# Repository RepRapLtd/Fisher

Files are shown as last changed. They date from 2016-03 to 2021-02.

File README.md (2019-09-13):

# Fisher Delta 3D printer
RepRap Fisher Delta 3D printer design files
Repository includes all design files for the current Fisher Delta 3d printer kit designed by [eMAKER](https://emaker.io/product/fisher-3d-printer-kit/) and manufactured and sold by [RepRapLtd](https://reprapltd.com/product-category/3d-printers/).

Organised into the following folders:

* sw/ Original design files in Solidworks 2016 format. The latest design is in FreeCAD.
* stl/ Printable files.
* dxf/ Lasercut files.
* step/ Designs in ISO STEP format.
* FreeCAD/ Designs for the FreeCAD CAD system.
* InDevelopment/ What it says...
* Legacy/ Old files no longer current.
* SoftwareXXX/ Current firmware as a compiled .bin file from [David Crocker](https://github.com/dc42/RepRapFirmware/releases) and [Duet3d](https://duet3d.dozuki.com/Wiki/Firmware_Overview) plus SD card images.

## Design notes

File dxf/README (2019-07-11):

Editing .dxfs
-------------

Before save:

  1. Select all.
  2. Modify attributes-
       Layer: 0
       Colour: Black/white
       Line width: 0.15mm
       Line type: continuous
  3. Save

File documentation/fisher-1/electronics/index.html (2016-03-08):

# Electronics

# Side panel wiring

You will need the following parts:

# | Component | Qty | Type

1303 | Side Panel | 1 | Laser cut
242 | M3x16mm cap head screw | 6 | Fastener
185 | Microswitch | 2 | Electronics
133 | Cable ties 2mm | as needed | Electronics
585 | Hot end loom – 1190mm | 1 | Wiring
1198 | End stop loom – 500mm | 1 | Wiring
552.1 | End stop loom – 600mm | 1 | Wiring
1199 | End stop loom – 800mm | 1 | Wiring
789 | Motor wiring loom – 500mm | | Wiring

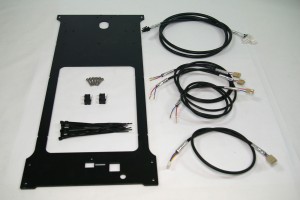
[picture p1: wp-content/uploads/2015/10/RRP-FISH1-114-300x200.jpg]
RRP-FISH1-114

(http://emaker.github.io/Fisher/wp-content/uploads/2015/10/hot-end-loom-components.jpg)

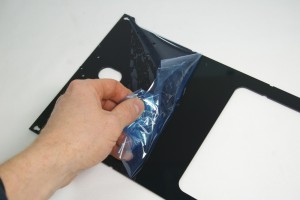
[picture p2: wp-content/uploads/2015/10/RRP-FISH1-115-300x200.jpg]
RRP-FISH1-115
Remove the protective film from the acrylic panel. | 
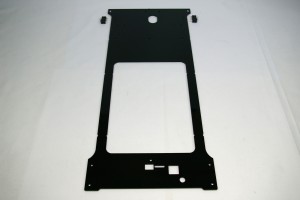
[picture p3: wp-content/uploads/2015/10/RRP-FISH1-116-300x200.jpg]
RRP-FISH1-116
The microswitches fit to the inside of the panel. Note the orientation of the bottom of the panel; this fits around the Duet electronics. | 
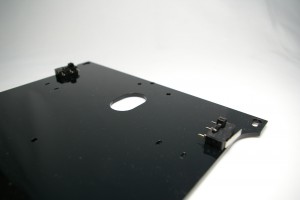
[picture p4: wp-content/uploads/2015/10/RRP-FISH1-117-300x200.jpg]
RRP-FISH1-117
Fit the microswitches with cable ties, as you did with the first microswitch. Make sure the cable tie end is towards the top of the panel. | 
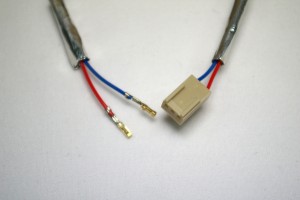
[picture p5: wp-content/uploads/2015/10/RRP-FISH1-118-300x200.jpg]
RRP-FISH1-118
The endstop looms have two wire, and there are three different lengths. | 
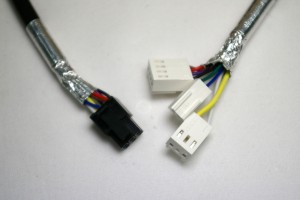
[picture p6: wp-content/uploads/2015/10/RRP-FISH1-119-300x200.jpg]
RRP-FISH1-119
The hot end loom has eight wires. | 
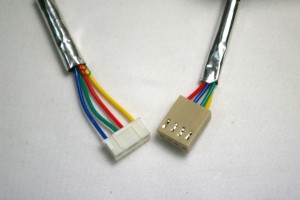
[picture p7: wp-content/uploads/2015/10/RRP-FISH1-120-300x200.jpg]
RRP-FISH1-120
The extruder motor wire has four wires. | 
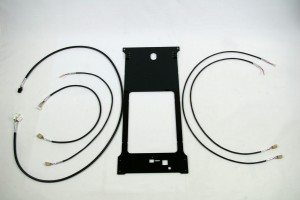
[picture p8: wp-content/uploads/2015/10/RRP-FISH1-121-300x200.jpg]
RRP-FISH1-121
Mount the shortest endstop loom, the hot end loom and the extruder motor loom on the left side. The other two endstop looms go on the right. | 
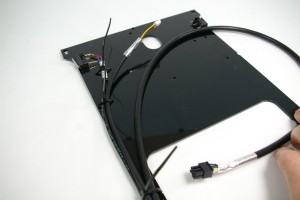
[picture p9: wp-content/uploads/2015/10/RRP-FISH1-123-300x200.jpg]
RRP-FISH1-123
Left side: Attach the endstop loom to the microswitch on the left hand side. Put the crimps on the outside tabs of the microswitch, NOT the middle one. Polarity is not important. Try not to bend the crimps on the microswitch tabs, or they will become loose. | 
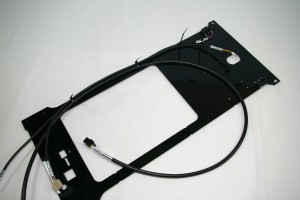
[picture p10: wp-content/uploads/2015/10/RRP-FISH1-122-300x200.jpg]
RRP-FISH1-122
Fasten the endstop loom in the top cable tie, the endstop and the extruder loom in the next one down, and all three looms in the rest of the cable ties. Don’t fully tighten the cable ties yet, so you can adjust the wire position. | 
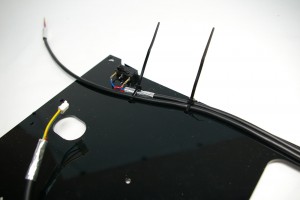
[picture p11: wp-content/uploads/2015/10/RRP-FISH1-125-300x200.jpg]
RRP-FISH1-125
Right side: connect the shorter endstop loom to the microswitch. | 
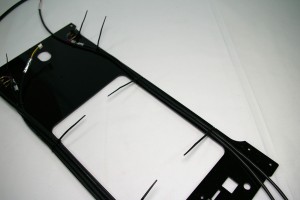
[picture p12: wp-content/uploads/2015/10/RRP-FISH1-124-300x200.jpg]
RRP-FISH1-124
Cable tie both wires in all of the positions. | 
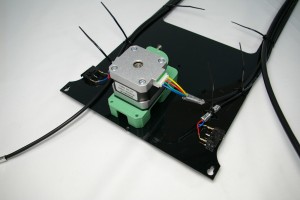
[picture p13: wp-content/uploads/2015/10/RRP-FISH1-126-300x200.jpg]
RRP-FISH1-126
Attach the extuder to the panel, with two M3x16mm cap head screws, from the outside. Connect the extruder motor loom to the extruder motor. | 

## Fit the panel and connect

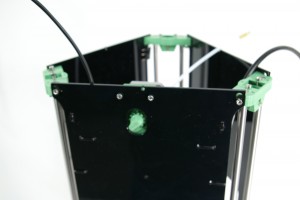
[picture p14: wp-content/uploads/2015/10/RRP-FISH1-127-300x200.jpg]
RRP-FISH1-127
As with the other panels, lift the printer up off the surface, and fit the top of the panel onto the screws in the idler printed part. | 
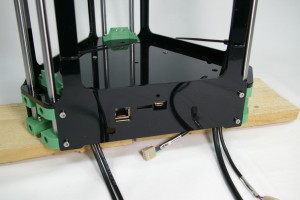
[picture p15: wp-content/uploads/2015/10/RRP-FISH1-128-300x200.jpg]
RRP-FISH1-128
Line up the bottom with the holes in the motor mounts, and fasten with four M3x16mm cap head screws. Make sure the wiring looms fit into the slots in the base plate. | 
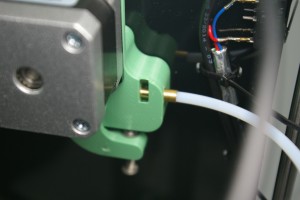
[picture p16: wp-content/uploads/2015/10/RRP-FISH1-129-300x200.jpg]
RRP-FISH1-129
Connect the Bowden tube to the extruder. Remove the tongue, and insert the brass union. | 
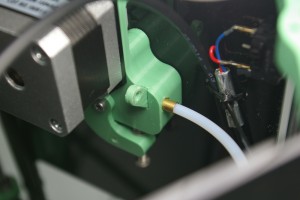
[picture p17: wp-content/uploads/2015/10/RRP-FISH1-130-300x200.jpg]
RRP-FISH1-130
Reinsert the tongue. This should engage with the slot in the brass union. | 
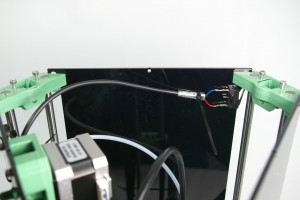
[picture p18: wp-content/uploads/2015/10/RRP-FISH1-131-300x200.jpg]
RRP-FISH1-131
Connect the third microswitch in the same way as the other two, and cable tie it to the panel. | 
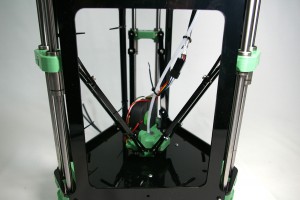
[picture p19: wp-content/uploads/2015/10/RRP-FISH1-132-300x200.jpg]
RRP-FISH1-132
Connect the hot end loom to the hot end. We find it useful to cable tie the loom loosely to the Bowden tube, above and below the connector. | 
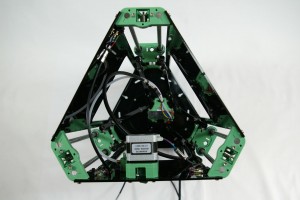
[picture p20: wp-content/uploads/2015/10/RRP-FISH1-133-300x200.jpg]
RRP-FISH1-133
Now adjust the cable lengths until everything is neat. The hot end loom and Bowden tube should move together. Try and get a nice loop, so they concertina up as the effector moves up. | 
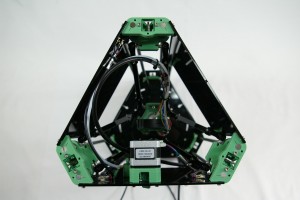
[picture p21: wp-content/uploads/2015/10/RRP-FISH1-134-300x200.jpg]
RRP-FISH1-134
Tighten and trim all of the cable ties. Move the carriages up and down their full range of movement, making sure they don’t catch on anything. Check that the heads of the cable ties don’t get in the way, and that the wiring looms are neat against the side panels. Adjust any cables as needed, and make sure the hot end loom and Bowden tube don’t catch on anything. | 

# Bed probe wiring

You will need the following parts:

# | Component | Qty | Type

1203 | Bed probe loom | 1 | Wiring
1202 | Bed probe wire | 2 | Wiring
242 | M3x16mm cap head screw | 6 | Fastener
212 | M3 washer | 6 | Fastener
1253 | M3x8mm spacer | 6 | Hardware

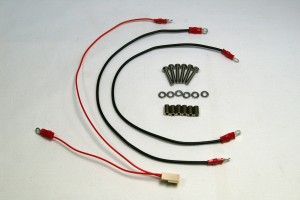
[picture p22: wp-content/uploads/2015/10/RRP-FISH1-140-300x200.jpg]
RRP-FISH1-140


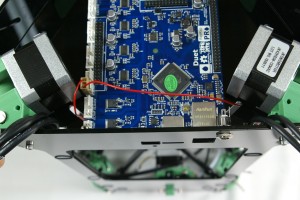
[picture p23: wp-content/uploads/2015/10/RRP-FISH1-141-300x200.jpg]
RRP-FISH1-141
Fit the bed probe loom 3-way connector to the E-stop header on the Duet. Push the wires through the slots in the base, as shown. The long wire can go under the Duet, if you prefer. | 
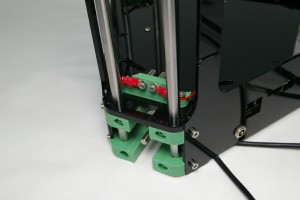
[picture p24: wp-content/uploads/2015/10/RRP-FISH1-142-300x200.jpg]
RRP-FISH1-142
Attach the ring terminals of the bed probe loom and bed probe wires to the bed mounting brackets. For each connection, the order is M3x16mm cap head screw, ring terminal of loom, bed mounting bracket, M3 washer, round spacer. | 
View from the front of the bed mounting bracket. | RRP-FISH1-143
Repeat the above steps for all six connections. The circuit goes around the circle. The balls on the print surface will complete the circuit (see later). When the nozzle pushes down on the bed, the circuit is broken. This calibrates the nozzle height. | RRP-FISH1-144

# Fit the power jack

You will need the following parts:

# | Component | Qty | Type

193 | Power jack | 1 | Electronics
455 | Power jack nut | 1 | Electronics

RRP-FISH1-138

Turn the printer over. It can rest on it’s top as you connect the wiring. The DC power jack may now be fitted as shown, next to the ethernet socket. | RRP-FISH1-139

# Duet connections

## Wiring diagram

The instructions below show the fitting of the wiring. If in doubt, refer to this wiring diagram.

FISHER-1-Duet0.6-109

## Duet wiring connections

Connect the wiring looms to the Duet, as shown in the pictures below (click on any picture for a larger version). Also refer to the wiring diagram, above. You will need the following parts:

# | Component | Qty | Type

1201 | DC cable – 250mm | 1 | Wiring
477 | Motor loom – 160mm | 1 | Wiring
478 | Motor loom – 90mm | 2 | Wiring

RRP-FISH1-145

FAN0 – NO CONNECTION! Do not connect anything to the first two pins on the left. They are not used on the Fisher. | RRP-FISH1-146
E0_TEMP – Hot end thermistor (green/blue, 2-way) | RRP-FISH1-147
E0_HEATER – Hot end heater (black/purple/red/brown, 4-way) | RRP-FISH1-148
– Hot end fan (yellow/none/white, 3-way) NOTE: this connects to the double row of pins, NOT to ‘FAN0’. From the left, there should be two clear pins, then the yellow wire, another pin (covered by the housing, but not connected), then the white wire. | RRP-FISH1-149
E0_MOT/STOP – (on first three pins) Bed probe (red/blank/red, 3-way). This was already fitted in the bed probe wiring step. | RRP-FISH1-149
E0_MOT/STOP – (on the other four pins) Extruder drive motor (yellow/green/blue/red, 4-way) | RRP-FISH1-150
X_MOT/STOP – X endstop (blue, space, red, 3-way) This is the SHORTEST endstop loom. | RRP-FISH1-151
X_MOT/STOP – (on the other four pins) X motor (black/green/blue/red, 4-way) Now connect the X motor to the Duet, using a 90mm motor loom. This is the motor closest to the motor connection pins on the Duet. Check that the endstop at the top of this tower is the one connected next to the X motor. | RRP-FISH1-152
Y_MOT/STOP – Y endstop (blue, space, red, 3-way) This is the LONGEST endstop loom. | RRP-FISH1-153
Y_MOT/STOP – (on the other four pins) Y motor (black/green/blue/red, 4-way) Next the Y motor, using a 90mm motor loom. This is the motor nearest the large screw terminals on the end of the Duet board. Check that the endstop at the top of this tower is the one connected next to the Y motor. | RRP-FISH1-154
Z_MOT/STOP – Z endstop (blue, space, red, 3-way) This is the MEDIUM length endstop loom. | RRP-FISH1-155
Z_MOT/STOP – (on the other four pins) Z motor (black/green/blue/red, 4-way) Now the Z motor, using the 160mm motor loom. This is the motor nearest the ethernet socket on the Duet. Check that the endstop at the top of this tower is the one connected next to the Z motor. | RRP-FISH1-157
All the wiring connections fitted. | RRP-FISH1-156
This picture shows the motor connections, and orientation. If you have put the motor on the wrong way around, you can turn the motor around, to make the motor wiring easier. Unscrew the four motor screws, and turn the motor around, then retighten the screws. | RRP-FISH1-158
Finally, connect the DC power cable. One of the cores has a black stripe running along it’s length. Connect this to the negative terminal (on the left hand side as viewed in the photograph). | RRP-FISH1-159
Connect the DC power cable to the tabs on the back of the jack. | RRP-FISH1-160
Ground is the centre of the three tabs (the wire with the black stripe should connect to this), and positive is the tab that connects to the centre pin. Fit them with the ‘curly’ part of the crimp outwards. | HUX2-electronics-25
With all the wiring fitted, tidy up the wiring so that it all fits below the level of the acrylic side panels. You can use a couple of cable ties to help. | RRP-FISH1-161

# Jumper

You will need the following parts:

# | Component | Qty | Type

| Fisher | 1 | Part-assembled
285 | PCB Jumper | 1 | Electronics

RRP-FISH1-162

Fit the jumper onto the 5V_EN (JP9) header pins (location highlighted in the picture). This uses the on-board 5V regulator to supply power to the main processor of the Duet, when 19V power is connected. | RRP-FISH1-163
A close up of the jumper position. | RRP-FISH1-164

Fisher Delta 3D printer © 2016. All Rights Reserved.

Powered by WordPress (http://www.wordpress.org). Designed by Woo Themes (http://www.woothemes.com)

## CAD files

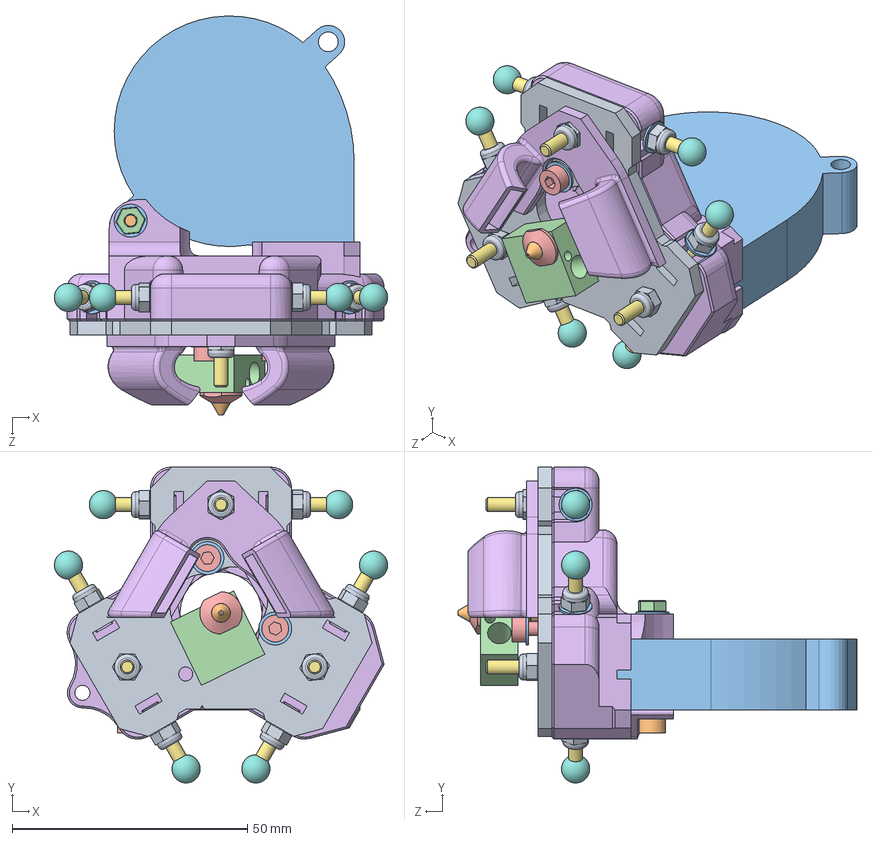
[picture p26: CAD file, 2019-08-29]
sw/head.sldasm
70.8 x 67.2 x 84.8 mm
heater-block

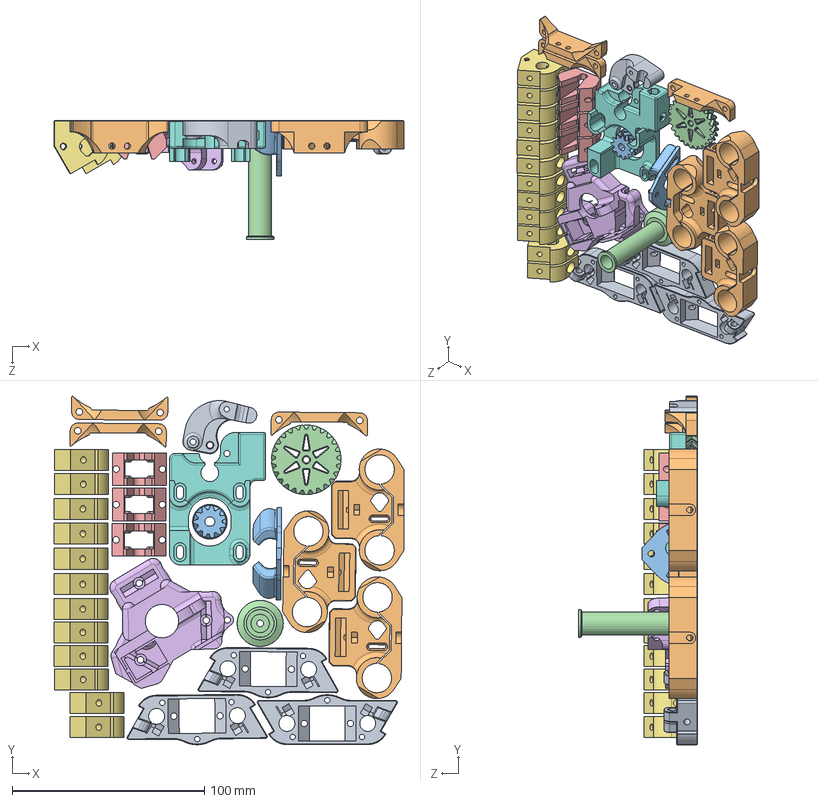
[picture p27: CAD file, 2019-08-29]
sw/1312.SLDASM
181.9 x 181.2 x 62.0 mm

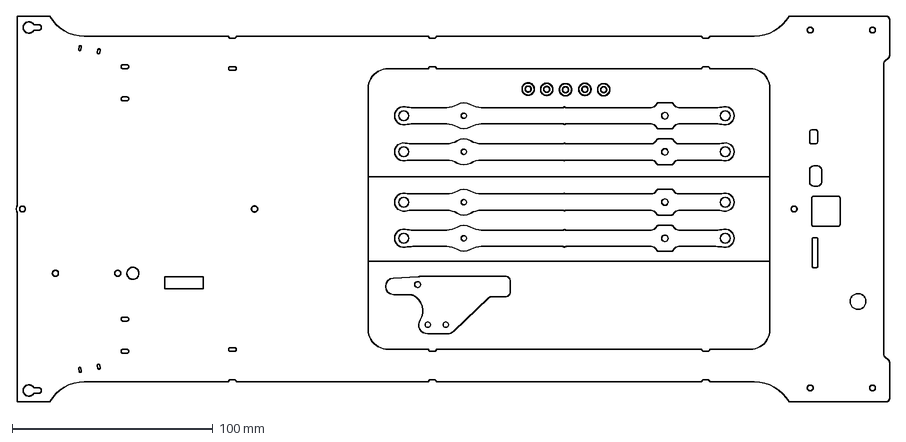
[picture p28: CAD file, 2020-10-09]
dxf/1196.3.dxf
434.6 x 192.0 mm

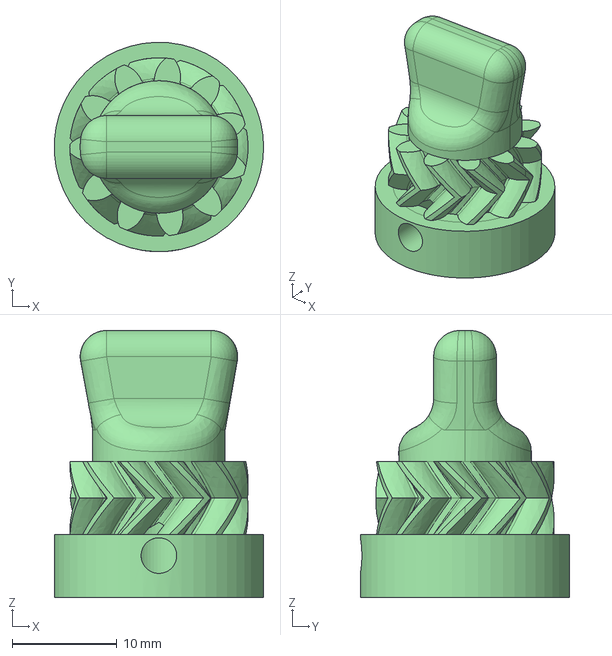
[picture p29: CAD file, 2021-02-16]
FreeCAD/1310.2.FCStd
20.0 x 20.0 x 25.5 mm

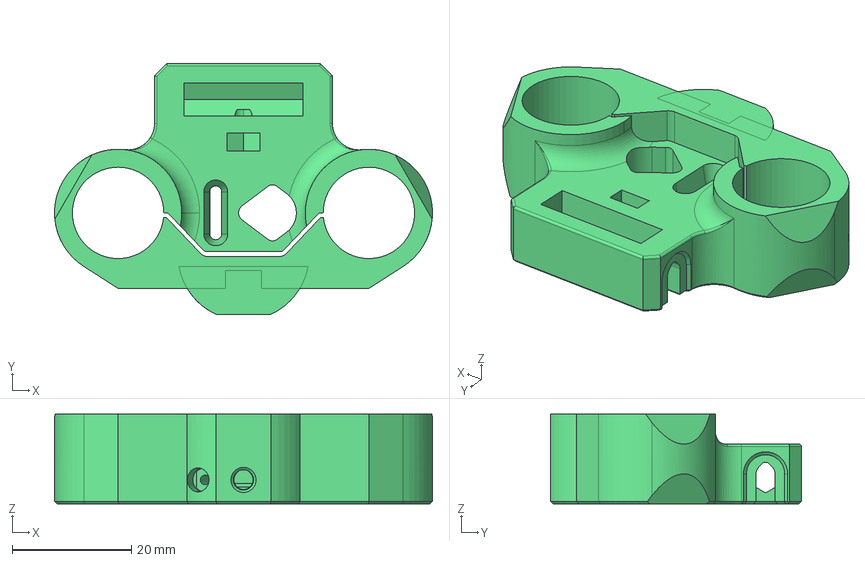
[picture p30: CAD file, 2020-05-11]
InDevelopment/Mechanics/1304.2.FCStd
63.3 x 42.0 x 15.0 mm

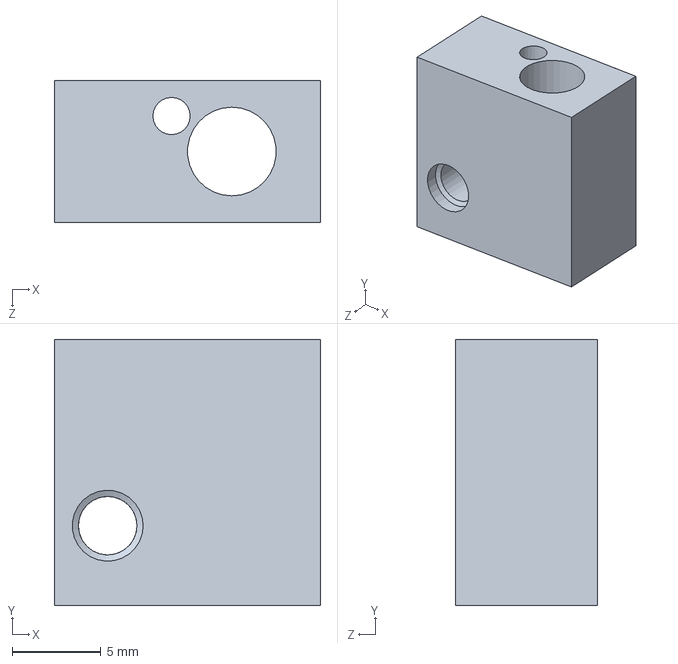
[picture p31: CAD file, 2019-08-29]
sw/heater-block.SLDPRT
15.0 x 15.0 x 8.00 mm

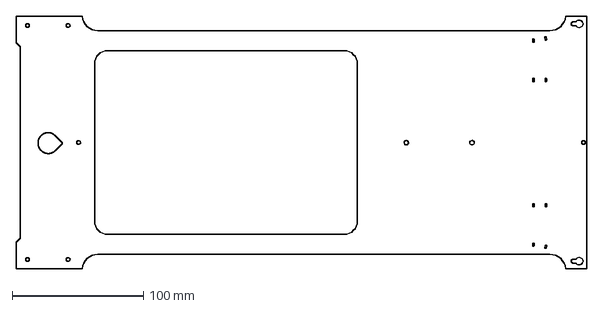
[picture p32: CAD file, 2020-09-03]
dxf/#1302.1.dxf
434.2 x 192.1 mm

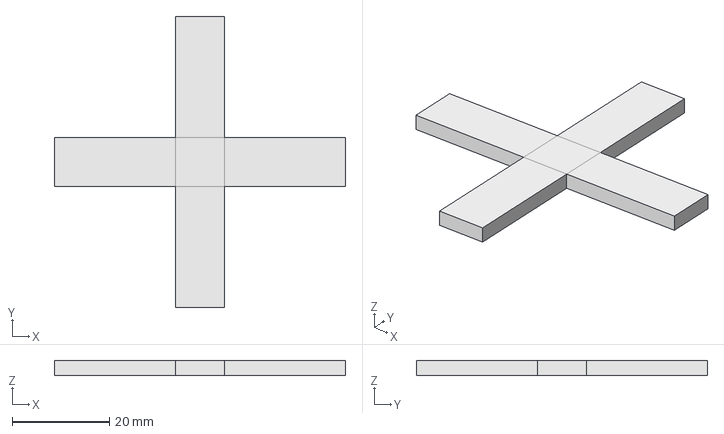
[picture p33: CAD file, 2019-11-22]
FreeCAD/test-cross.fcstd
60.0 x 60.0 x 3.00 mm

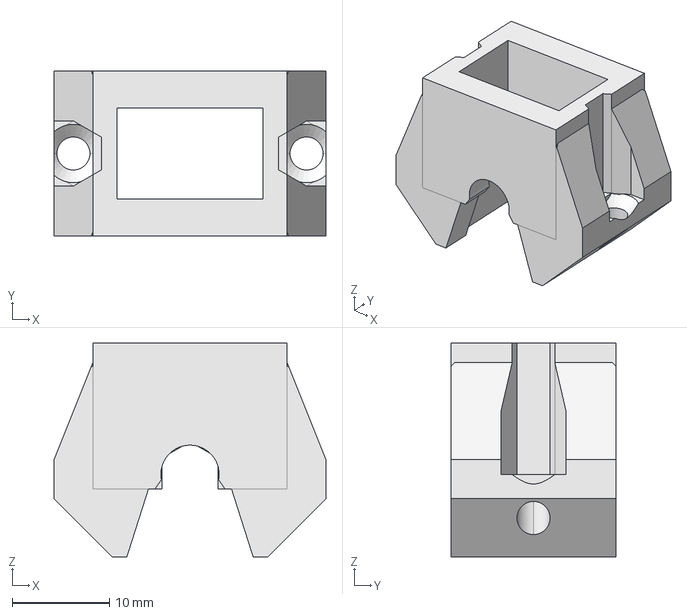
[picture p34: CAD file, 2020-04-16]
InDevelopment/Mechanics/1243.1.FCStd
28.0 x 17.0 x 22.0 mm

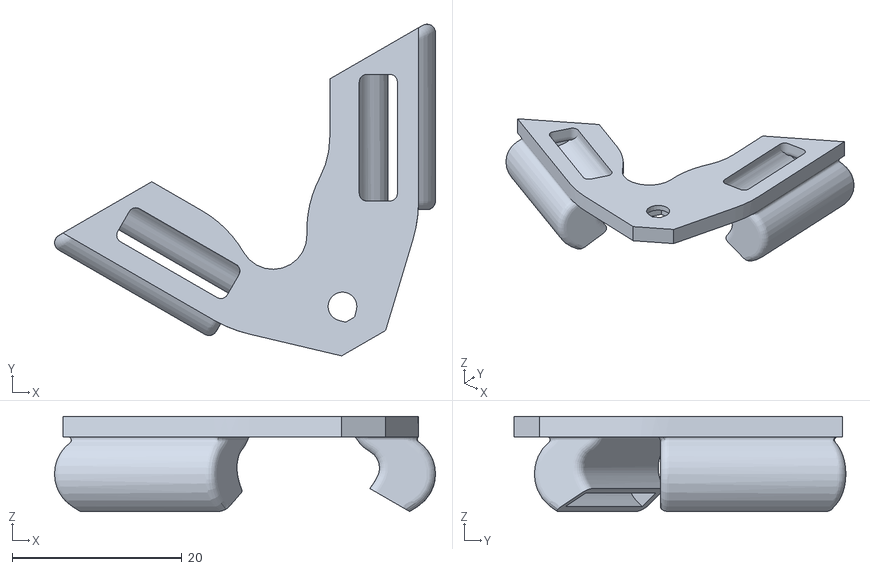
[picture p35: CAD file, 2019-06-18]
stl/1247.1 Nozzle Duct.stl
45.0 x 39.1 x 11.2

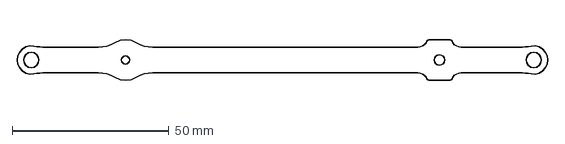
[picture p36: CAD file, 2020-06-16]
dxf/1232.2.dxf
169.5 x 13.6 mm

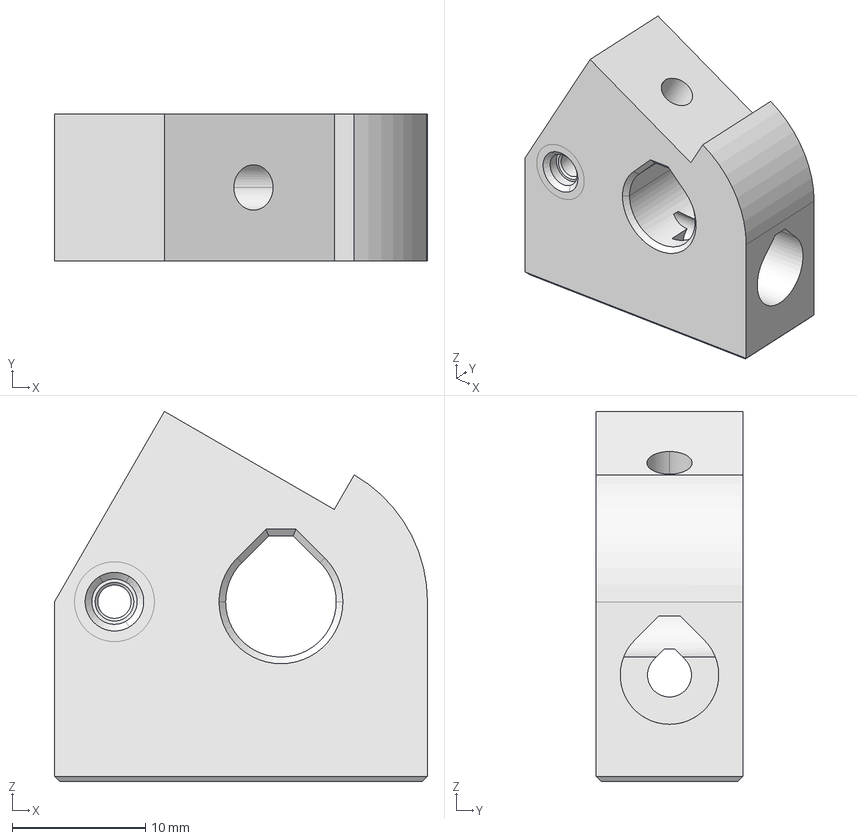
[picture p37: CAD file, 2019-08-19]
FreeCAD/1305.1.fcstd
28.0 x 11.0 x 27.8 mm

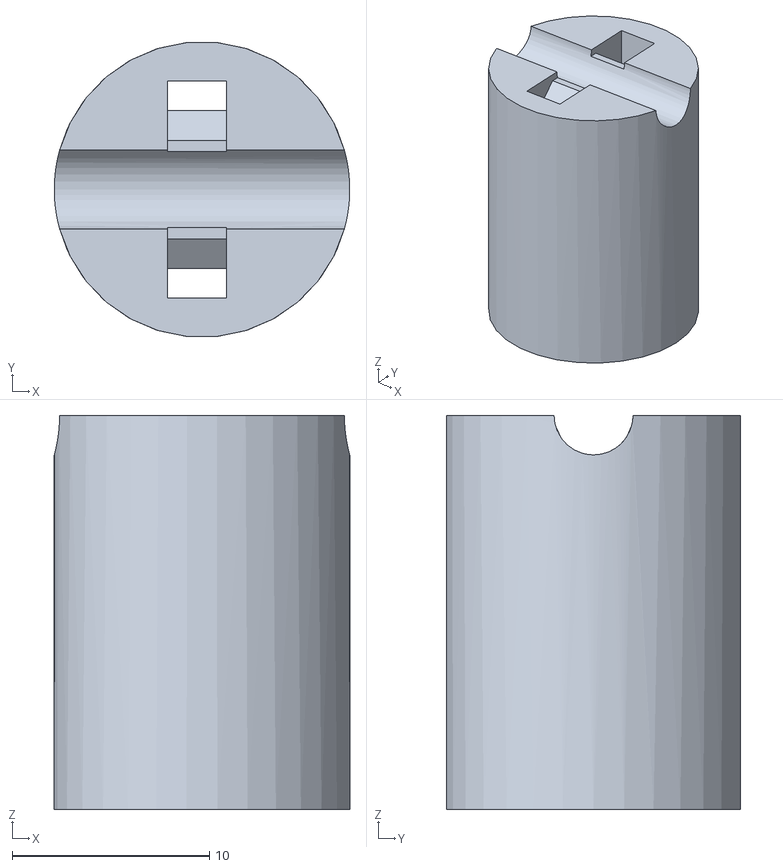
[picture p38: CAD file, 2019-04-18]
stl/6199-filament-guide-spacer.stl
15.0 x 14.9 x 20.0

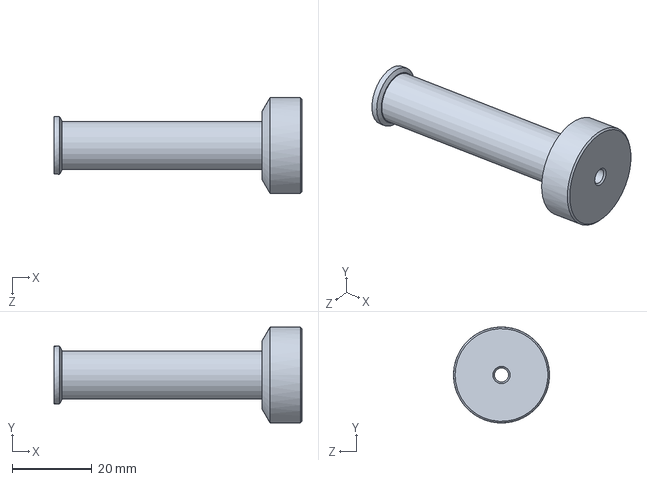
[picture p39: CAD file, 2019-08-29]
sw/1249.SLDPRT
62.0 x 24.0 x 24.0 mm

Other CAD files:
stl/1310.2-small-gear with grip.STL
dxf/1195.3.dxf
FreeCAD/6197 masterspool-spigot.fcstd
stl/1310.1-small-gear with grip.STL
InDevelopment/Mechanics/STLs/1243.1.stl
InDevelopment/Mechanics/STLs/1304.2.stl
Legacy/Old DXF/#1195 - 05.DXF
Legacy/Old DXF/#1223.DXF
Legacy/Old DXF/1195 - 05 - single.DXF
Legacy/Old DXF/1195 - 05.DXF
Legacy/Old DXF/1195.1.dxf
Legacy/Old DXF/1195.2.dxf
Legacy/Old DXF/1196 - 07 - single.dxf
Legacy/Old DXF/1196 - 07.dxf
Legacy/Old DXF/1196.1.dxf
Legacy/Old DXF/1232-fisher-rods-x2.dxf
Legacy/Old DXF/1232.1-fisher-rods-x2.dxf
Legacy/Old DXF/1232.1-fisher-rods-x6.dxf
Legacy/Old DXF/1232.1.dxf
Legacy/Old DXF/1232.DXF
Legacy/Old DXF/1302.DXF
Legacy/Old DXF/1303.DXF
Legacy/Old-STL/1249.STL
Legacy/Old-STL/1305.STL
Legacy/Old-STL/rod-end.STL
Legacy/old-sd-image/stl/Robot.stl
dxf/#1195 - 05.DXF
dxf/#1223.DXF
dxf/1195 - 05 - single.1.dxf
dxf/1195 - 05 - single.DXF
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

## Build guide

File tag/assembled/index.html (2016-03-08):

# Tag Archives: Assembled

 (http://emaker.github.io/Fisher/author/jeanmarc/) Nov 20 2015

# Assembled Fisher Delta 1.0 for Christmas (http://emaker.github.io/Fisher/assembled-fisher-delta/)

- Fisher 1 (http://emaker.github.io/Fisher/category/fisher-1/), News (http://emaker.github.io/Fisher/category/news/)
- Assembled (http://emaker.github.io/Fisher/tag/assembled/), fisher (http://emaker.github.io/Fisher/tag/fisher/)
- Leave a comment (http://emaker.github.io/Fisher/assembled-fisher-delta/#respond)

We have a limited number of Assembled Fisher Delta 1.0 RepRap 3D printers available to order for dispatch in time for Christmas – So get your order in quick! For a special price of £449 (ex VAT) you will receive a fully built Fisher 1.0 which has been commissioned and tested. The assembled kits will […]

Fisher Delta 3D printer © 2016. All Rights Reserved.

Powered by WordPress (http://www.wordpress.org). Designed by Woo Themes (http://www.woothemes.com)

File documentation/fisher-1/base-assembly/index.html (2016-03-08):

# Base assembly

# Goal

TIP: Click on pictures in the instructions to see a larger version. Right-click and select ‘Open link in new Tab’ to see the full size image.

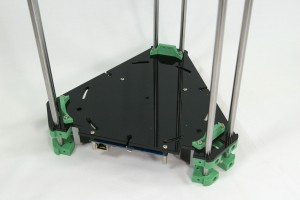
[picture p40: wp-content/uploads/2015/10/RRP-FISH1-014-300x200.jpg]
RRP-FISH1-014
By the end of this section, you will have assembled the base of the printer. | 

# Tower assembly

There are three towers, that support the three moving arms of the printer. You will need the following parts:

# | Component | Qty | Type

934 | Smooth rod 8mm x 426mm | 2 | Hardware
408 | NEMA 17 stepper motor | 1 | Hardware
1305 | Motor bracket | 4 | Printed
112 | M3x25mm cap head screw | 4 | Fastener
212 | M3 plain washer | 4 | Fastener

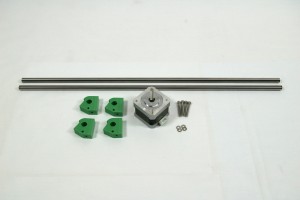
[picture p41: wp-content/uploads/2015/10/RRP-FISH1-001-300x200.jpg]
RRP-FISH1-001


TIP: There’s a list of the Fisher 1 printed parts on THIS PAGE (https://reprappro.com/documentation/fisher-1/#Printing_parts_for_Fisher). Click on the ‘Location’, to see a preview of the printed part, if you’re not sure what it is.

NOTE: The ground bars should have clean chamfered ends, free from burrs, so they can slide easily into the relevant parts without causing any damage. Check all the ground bars before proceeding and file any burrs away as necessary. You may damage the linear bearings when you fit them if you do not do this.

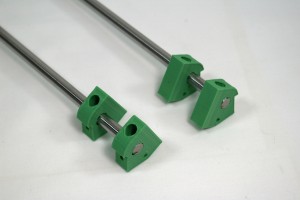
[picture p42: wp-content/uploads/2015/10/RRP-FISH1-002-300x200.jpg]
RRP-FISH1-002
Push two printed motor brackets onto the end of each smooth rod. Note the orientation, and that the bracket closest to the end of the rod should be flush with the end. | 
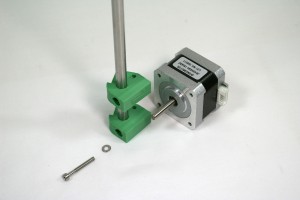
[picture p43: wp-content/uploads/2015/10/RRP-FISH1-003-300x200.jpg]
RRP-FISH1-003
Screw a M3x25mm cap head screw, through a washer and the motor bracket, and into the motor. Note that the motor wiring connector should come out sideways, not up or down. | 
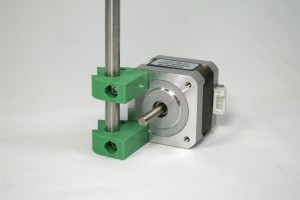
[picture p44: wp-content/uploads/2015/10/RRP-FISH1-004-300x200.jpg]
RRP-FISH1-004
Add a second M3x25mm cap head screw into the top bracket. Slide motor bracket so it lines up with the hole in the motor, and tighten. | 
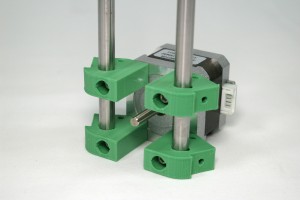
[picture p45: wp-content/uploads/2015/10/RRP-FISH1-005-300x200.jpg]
RRP-FISH1-005
Repeat for the other side. The screws and washers, when tightened, hold the rods in place so they cannot slip through the motor bracket. | 
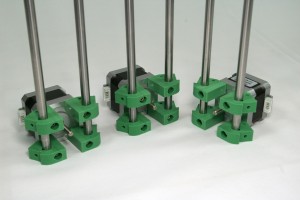
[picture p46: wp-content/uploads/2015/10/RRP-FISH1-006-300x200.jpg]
RRP-FISH1-006
You need to build three towers in total, so repeat the above twice more. You will need two with motor wiring connectors on one side, and one with it on the other side. See the picture for orientation. | 

# Base plate assembly

The base plate holds the electronics. You will need the following parts:

# | Component | Qty | Type

1299 | Base Plate (5mm acrylic) | 1 | Laser cut
744 | Duet PCB spacer (5mm acrylic, part of base plate) | 4 | Laser cut
394 | Duet PCB | 1 | Electronics
581 | Female/Female Hex Spacer | 4 | Electronics
1186 | M3x16mm button head screw | 4 | Electronics
212 | M3 plain washer | 4 | Fastener

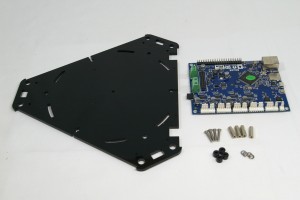
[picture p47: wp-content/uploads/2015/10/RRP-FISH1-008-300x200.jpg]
RRP-FISH1-008


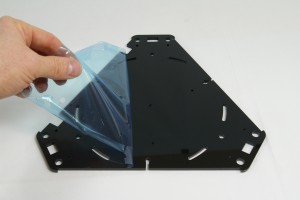
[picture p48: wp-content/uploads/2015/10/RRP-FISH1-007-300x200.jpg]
RRP-FISH1-007
All acrylic parts are covered by a protective film, on both sides. Always remove this before assembly. The Duet PCB spacers are cut into the base plate, and are attached by a small sprue. Remove them for assembly. | 
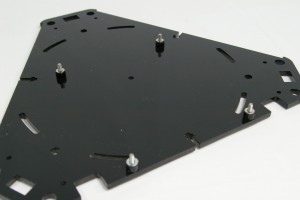
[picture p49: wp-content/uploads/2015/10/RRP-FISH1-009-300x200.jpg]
RRP-FISH1-009
There are four holes in the base plate, for mounting the Duet PCB. Push an M3x16mm button head screw through each one, and put a Duet PCB spacer and M3 washer on each on. | 
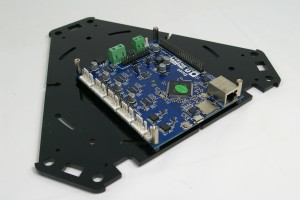
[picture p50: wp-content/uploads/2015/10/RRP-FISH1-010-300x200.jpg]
RRP-FISH1-010
Place the Duet on these, as shown. Fasten the Duet in place with the four Female/Female hex spacers. | 

# Base assembly

Assemble the lower part of the printer. You will need the following parts:

# | Component | Qty | Type

| Motor towers | 3 | Assembled
| Base | 1 | Assembled
1245 | Kinematic Mount | 3 | Printed
242 | M3x16mm cap head screw | 6 | Fastener

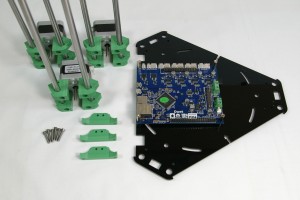
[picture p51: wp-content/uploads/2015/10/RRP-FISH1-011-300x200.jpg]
RRP-FISH1-011


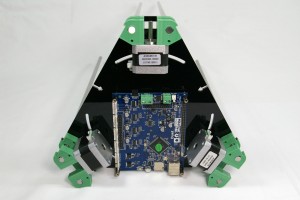
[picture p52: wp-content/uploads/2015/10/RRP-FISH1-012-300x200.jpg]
RRP-FISH1-012
Push the motors up through the base plate. Be careful to support the rods when doing this; acyrlic can be quite brittle, so you don’t want the ends to move around. Note the orientation of the motor connectors to the Duet; fit them as shown will make wiring them up much easier. | 
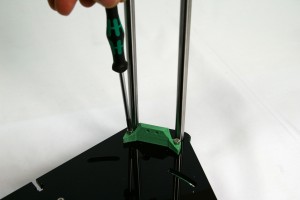
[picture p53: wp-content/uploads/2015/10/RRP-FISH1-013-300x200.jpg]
RRP-FISH1-013
Using two M3x16mm cap head screws on each, screw the three kinematic mounts onto the base plate. The screws should self-tap into the plastic of the printed motor mount underneath. | 
Your printer should now look like this. | RRP-FISH1-014

Fisher Delta 3D printer © 2016. All Rights Reserved.

Powered by WordPress (http://www.wordpress.org). Designed by Woo Themes (http://www.woothemes.com)

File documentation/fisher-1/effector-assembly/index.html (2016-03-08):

# Effector assembly

# Goal

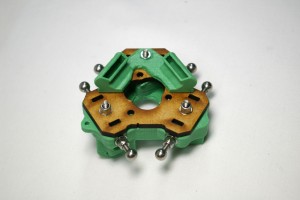
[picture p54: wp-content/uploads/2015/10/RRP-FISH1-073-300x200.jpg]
RRP-FISH1-073
By the end of this section, you will have built the effector. | 

# Effector

The effector carries the hot end, and is moved in three dimensions by the movement of the carriages on the towers. You will need the following parts:

# | Component | Qty | Type

1301 | Effector | 1 | Printed
1247.1 | Nozzle Duct | 1 | Printed
1223 | Effector Plate (MDF) | 1 | Laser cut
242 | M3x16mm cap head screw | 6 | Fastener
257 | M3x12mm cap head screw | 3 | Fastener
204 | M3 Nylock nut | 8 | Fastener
212 | M3 plain washer | 8 | Fastener
258 | M3 nut | 3 | Fastener
1191 | 6mm Threaded steel ball | 6 | Hardware

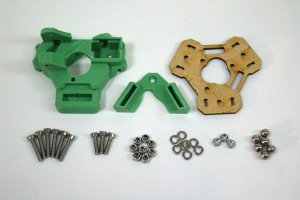
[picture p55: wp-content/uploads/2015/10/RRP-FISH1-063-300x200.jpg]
RRP-FISH1-063


## Connecting rod joints

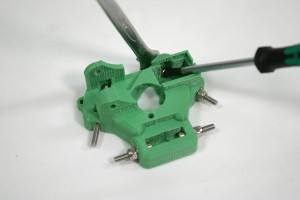
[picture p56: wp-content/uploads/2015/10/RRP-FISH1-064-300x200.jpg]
RRP-FISH1-064
Take the printed effector, and fit six M3x16mm cap head screws, each secured with an M3 washer and M3 Nylock nut, similar to the carriage. | 
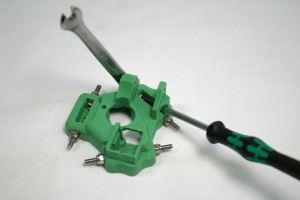
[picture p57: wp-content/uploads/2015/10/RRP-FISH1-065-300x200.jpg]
RRP-FISH1-065
Access to the M3x16mm cap head screws is possibly even more difficult than with the carriages. It really helps having a ball-ended Allen key! Tighten them as with the carriage assembly. | 
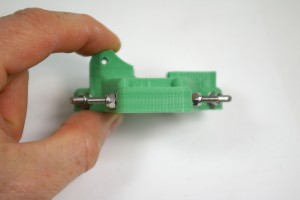
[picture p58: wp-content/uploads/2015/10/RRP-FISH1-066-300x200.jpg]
RRP-FISH1-066
As with the carriages, check that the screws are flat and straight. | 

Screw on a 6mm threaded steel ball to each side. As before, make sure the balls are free from swarf inside, and that they are threaded. Fully screw the balls on, then check that the outside measurement of the balls is close (+/- 0.25mm for best accuracy) to 56mm. You can tighten the Nyloc on the screw to pull the ball out a little, if necessary. If too wide, remove the ball and file down the screw a little, then replace the ball and measure.
NOTE: Kits supplied after 1st November 2015 have steel balls that are not tapped as deeply as previous versions. The outside measurement with these balls will be a little wider, at around 57mm.

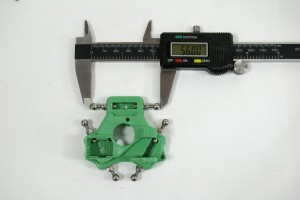
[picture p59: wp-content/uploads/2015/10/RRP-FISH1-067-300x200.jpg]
RRP-FISH1-067


The precise distance between the balls is actually not that important. What is important is that the distance between the balls on the carriage (see earlier in the instructions), and those on the effector should be the same, as close as possible. The rods that connect the carriage and effector must be parallel, so that the movement of the effector is always square to the carriage. If the distance between the balls is not the same, the rods will not be parallel, and the movement of the effector and hot end will not be consistent, and you may end up printing parts that are not dimensionally accurate.

## Effector plate

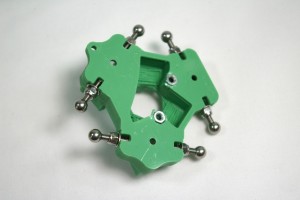
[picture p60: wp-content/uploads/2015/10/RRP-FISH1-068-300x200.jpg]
RRP-FISH1-068
Turn the effector over, and fit two M3 nuts in the captive holes underneath. | 
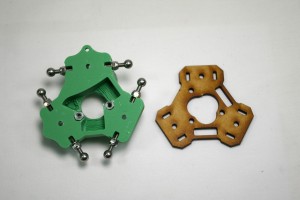
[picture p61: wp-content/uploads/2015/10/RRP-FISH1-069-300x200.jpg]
RRP-FISH1-069
Take the MDF effector plate, and orientate it so that the holes line up with M3 nuts, and duct holes match the effector. It only fits correctly one way! | 
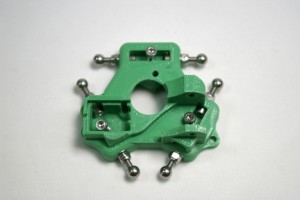
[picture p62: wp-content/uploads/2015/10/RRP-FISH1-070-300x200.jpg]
RRP-FISH1-070
From the top of the effector, put three M3x12mm cap head screws through the central holes, between the connecting rod joint screws. | 
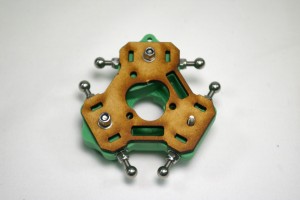
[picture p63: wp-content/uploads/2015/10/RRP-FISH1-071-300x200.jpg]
RRP-FISH1-071
Turn the effector back over, and fit the MDF effector plate, again making sure of the alignment. Use an M3 washer with M3 nylock nut on two of the screws, as shown. | 
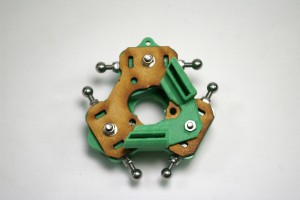
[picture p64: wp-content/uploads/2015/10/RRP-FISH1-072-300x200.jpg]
RRP-FISH1-072
Fit the fan duct on the final screw, with an M3 nut. Tighten all three screws to pull the effector together. | 

Fisher Delta 3D printer © 2016. All Rights Reserved.

Powered by WordPress (http://www.wordpress.org). Designed by Woo Themes (http://www.woothemes.com)

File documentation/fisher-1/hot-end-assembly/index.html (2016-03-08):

# Hot end assembly

# Goal

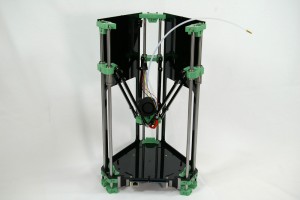
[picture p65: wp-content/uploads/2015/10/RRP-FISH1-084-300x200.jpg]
RRP-FISH1-084
By the end of this section, you will have built the hot end, assembled it with the effector, and installed it in the printer frame. | 

# Assemble the hot end components

The hot end melts the filament, and extrudes it, to build the 3D printed object.

## Nozzle assembly

The nozzle is where the filament is heated and extruded from. You will need the following parts:

# | Component | Qty | Type

1180 | Brass nut | 1 | Hot end
739 | Heater block | 1 | Hot end
1179 | Threaded nozzle | 1 | Hot end
1136 | Heatsink | 1 | Hot end

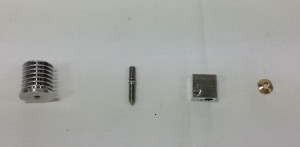
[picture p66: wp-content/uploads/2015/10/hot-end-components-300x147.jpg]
hot-end-components


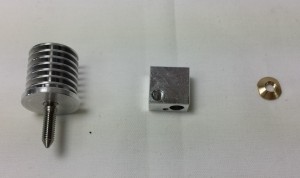
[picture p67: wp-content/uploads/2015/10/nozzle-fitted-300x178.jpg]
nozzle-fitted
Screw the nozzle into the base of the heatsink by hand. | 
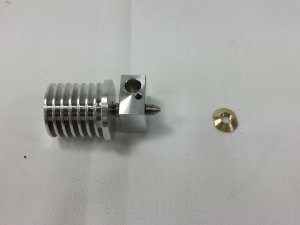
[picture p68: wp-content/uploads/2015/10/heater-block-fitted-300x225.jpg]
heater-block-fitted
Screw the heater block onto the nozzle, again by hand. There is not need to use any tools at this stage. Take care to fit the heater block with the small hole nearest the nozzle tip. | 
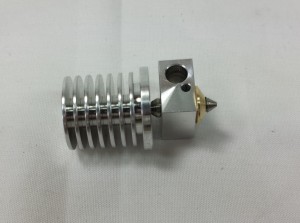
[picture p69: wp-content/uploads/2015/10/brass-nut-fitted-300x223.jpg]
brass-nut-fitted
Fit the brass nut. Using an 8mm spanner, gently tighten the assembly until it is just over ‘finger tight’. The constriction in the nozzle has a very thin wall, so care should be taken not to over tighten the assembly as it may result in snapping the nozzle. | 

## Bowden tube

The Bowden tube carries the filament to the hot end, from the extruder. You will need the following parts:

# | Component | Qty | Type

| Nozzle assembly | 1 | Assembled
1055 | Bowden tube | 1 | Hot end
106 | Bowden start | 1 | Hot end

Picture to come

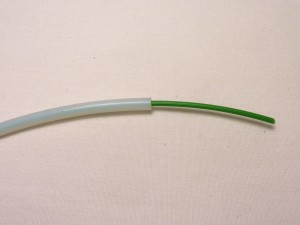
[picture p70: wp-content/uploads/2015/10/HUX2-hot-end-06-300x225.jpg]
HUX2-hot-end-06
Take the PTFE tube. Make sure the ends of the PTFE tube are cut square. (Filament has been inserted into tube just to show the tube against the background.) | 
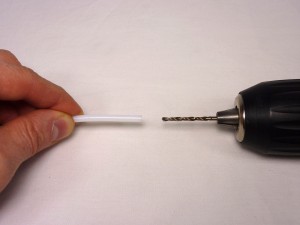
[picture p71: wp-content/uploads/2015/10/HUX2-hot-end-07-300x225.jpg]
HUX2-hot-end-07
You are going to screw the brass Bowden start and the heatsink onto each end of the tube. This will compress the PTFE tube’s inner hole. To allow the filament to run freely in the tube, you need to open out the ends of the PTFE tube first. Use a 2.5mm (2mm is too small, 3mm is too big) drill bit in a small hand chuck, or a slow electric drill. | 
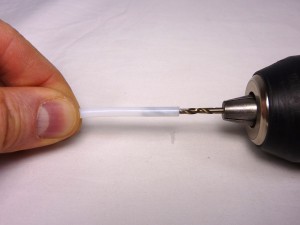
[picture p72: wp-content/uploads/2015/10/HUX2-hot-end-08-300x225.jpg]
HUX2-hot-end-08
Gently, and twisting clockwise all the time – never anti-clockwise, whether going in or coming out – use the drill bit to enlarge the inner hole in the PTFE, to a depth of around 15mm. Try to keep the drill as straight as possible into the tube. | 
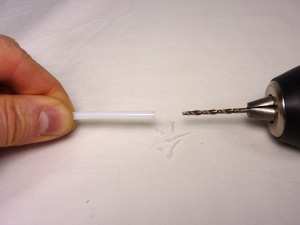
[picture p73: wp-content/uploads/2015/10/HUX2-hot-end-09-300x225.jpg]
HUX2-hot-end-09
Take several goes at it, going a couple of millimetres deeper each time and drawing the PTFE swarf out by keeping twisting clockwise and pulling. The drill should pull the PTFE swarf out with it. Repeat the process at the other end of the PTFE tube. | 
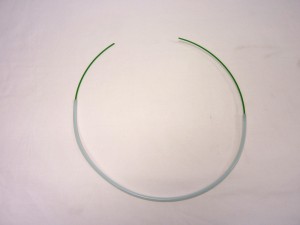
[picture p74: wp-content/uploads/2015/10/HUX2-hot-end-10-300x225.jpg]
HUX2-hot-end-10
IMPORTANT! The PTFE tube MUST BE CLEAR OF ALL PTFE SWARF before screwing the heatsink on! Push a piece of filament (use the 50cm piece you cut for the extruder testing) through the tube, which should push out any remaining PTFE swarf. Blow down the tube, from both ends, as well. It is very important to get any PTFE swarf out of the tube, otherwise this will end up in the nozzle the first time you print, blocking it! | 
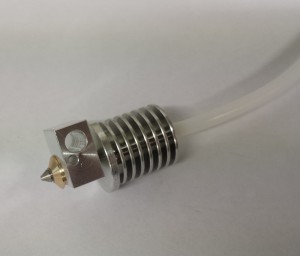
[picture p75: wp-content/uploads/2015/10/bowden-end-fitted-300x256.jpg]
bowden-end-fitted
Screw the tube into the heatsink as far as it will go, at which point the end of the tube will butt against the nozzle inside the heatsink. | 
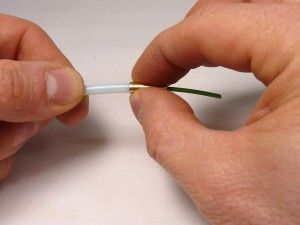
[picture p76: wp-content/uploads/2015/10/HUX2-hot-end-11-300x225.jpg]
HUX2-hot-end-11
Now you’re going to screw the brass Bowden end and the nozzle onto the PTFE tube. To help guide them onto the tube straight, put a piece of filament into the PTFE tube. This will keep the brass Bowden end (and nozzle) and PTFE tube axially in line; you don’t want them screwed on at an angle. Push the brass Bowden end up to the PTFE tube, and push while turning it clockwise. It will start to cut its own thread into the PTFE tube. | 
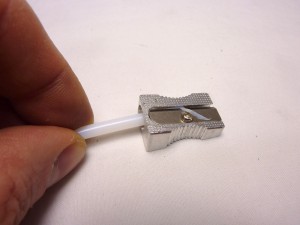
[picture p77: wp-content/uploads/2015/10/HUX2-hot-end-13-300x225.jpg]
HUX2-hot-end-13
If you have trouble getting the brass Bowden start started on tube, you can use a pencil sharpener to make a cone on the end of the tube. | 
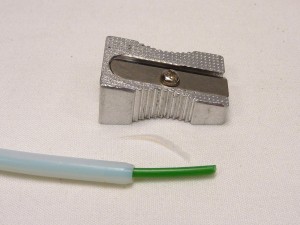
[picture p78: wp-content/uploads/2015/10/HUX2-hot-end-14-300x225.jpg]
HUX2-hot-end-14
Don’t cut too deeply with the pencil sharpener, which will make the cone too deep and long, or it will compress onto the filament when the brass Bowden start is screwed on. | 
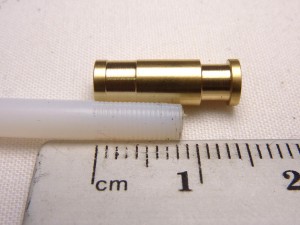
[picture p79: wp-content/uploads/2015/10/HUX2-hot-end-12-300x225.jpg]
HUX2-hot-end-12
Keep turning until the Bowden start will not screw on any further. If you then remove the brass union, you should see that the Bowden tube end has been threaded, to a depth of around 8mm. | 

## Thermistor

The thermistor is the temperature sensor for the hot end, and makes sure the hot end stays at the correct temperature. So it’s rather vital! You will need the following parts:

# | Component | Qty | Type

430 | Thermistor | 1 | Hot end
167 | PTFE heatshrink | 1 | Hot end

ORM-HotEndBuild-18

Cut the transparent PTFE heatshrink about 8mm shorter than the thermistor with its axial connecting wires. Put the thermistor in it so that 4mm of wire protrudes from each end. | ORM-HotEndBuild-18
Using a flame (a cigarette lighter, blowtorch, gas hob, or hot air gun work well; a hair dryer does not), shrink the heatshrink over the thermistor. Just waft the thermistor and heatshrink through the flame. You don’t want the heatshrink to overheat and to burn. | SANYO DIGITAL CAMERA
If you’re doing this with a cigarette lighter, hold the thermistor at one end, and heat the heatshrink from the middle out to the other end. The heatshrink will be transparent when it has fully shrunk, and will then go back to opaque when the heat is removed. Keep it above, not in, the flame, so it doesn’t overheat and go black. | ORM-HotEndBuild-20
Let it cool for a few moments, then turn it around and do the other side. Rolling the thermistor between your fingers while heating will improve the consistency of the heatshink. | ORM-HotEndBuild-23
Turn it around again and heat the first side, rolling it in your fingers, to get a really good, even heatshrink. Make sure it has shrunk properly around the central bulge, or it won’t fit easily into the heater block. | ORM-HotEndBuild-24
This is how the thermistor should look with the PTFE shrunk onto it. | ORM-HotEndBuild-25
Test the resistance of the thermistor with a multimeter. It should be around 100k ohms at an ambient temperature of 25C. Like the heated bed thermistor, the resistance will be greater if it is colder, and less if hotter. | HUX2-hot-end-29

## Test the cartridge heater

The cartridge heater provides the heat for the hot end. You will need the following parts:

# | Component | Qty | Type

314 | Cartridge heater 19v | 1 | Hot end

Picture to come

Check the resistance of the heater cartridge. It should be around 7.0 ohms. | HUX2-hot-end-30

## Thermistor wires

These wires connect the thermistor to the wiring loom.

# | Component | Qty | Type

433 | Thermistor wiring – 160mm | 2 | Hot end
197 | 2.4mm Black heatshrink | as needed | Hot end

New picture to come

If your thermistor wiring is supplied without heatshrink on both ends, and the female end looks like this, do the following. | RRP-thermistor-wiring-01
Fold in the two barbs that stick out the side, as shown in the first picture; a small screwdriver or tool with a point is easiest. They need to fold into the crimp, as they will hold the thermistor wire. | RRP-thermistor-wiring-02
Also flatten the top two tabs, so the crimp is smooth. If you put the heatshrink on with them sticking up, they can cut through the heatshrink, and cause a short circuit if they touch other metal. | RRP-thermistor-wiring-03
Put the heatshrink on the end of the wire, covering the crimp but leaving the end open. | RRP-thermistor-wiring-04
Check that it holds the thermistor firmly. You will cover the thermistor with high temperature PTFE heatshrink in the next step; you want as little metal showing as possible between the PTFE heatshrink and the black heatshrink, to avoid short circuits to metal parts of the printer. | RRP-thermistor-wiring-05

# Assemble the hot end and effector

The hot end is mounted in the effector. You will need the following parts:

# | Component | Qty | Type

| Hot end assembly | 1 | Assembled
| Effector assembly | 1 | Assembled
113 | M3x25mm hex head screw | 1 | Fastener
242 | M3x16mm cap head screw | 2 | Fastener
212 | M3 plain washer | 2 | Fastener
368 | 3×2 Female Housing (3020-06) | 1 | Hot end
314 | Cartridge heater 19v | 1 | Hot end
433 | Thermistor wiring -160mm | 2 | Hot end
| Thermistor (insulated) | 1 | Assembled
1194 | 50mm blower fan – 160mm crimped | 1 | Electronics
133 | Cable ties 2mm | 2 | Electronics

RRP-FISH1-074

Pull the thermistor through the heater block. If you use pliers, use them on the PTFE heatshrink, NOT on the metal legs of the thermistor; you are likely to break the thermistor. Ensure the thermistor bead is seated centrally inside the heater block. | RRP-FISH1-075
Push the hot end into the effector, orientated as shown. This may require a small amount of trimming of the printed effector part, but it is supposed to be a close fit. Do not trim the MDF effector plate; the hot end has a flange that sits on this. Bend the thermistor leg around the heater block; this ensures it can’t fall out. If the nozzle comes loose in the heatsink, taken the hot end out, tighten, and put it back in again. | RRP-FISH1-076
This picture shows the lower flange of the heatsink sitting on the MDF effector plate. | RRP-FISH1-078
Secure the hot end in place using the two M3x16mm cap head screws and M3 washers as shown. Take care to orient the heater block as shown, without loosening the nozzle in the heatsink, before tightening the M3 nuts. | RRP-FISH1-077

## Adding the heater, thermistor and fan

Connect the thermistor wires to the thermistor, and push the heater cartridge into the larger hole in the heater block. All wires should come out the same way. | RRP-FISH1-079
Fit the fan into the printed effector. It should be a snug fit. Using the M3x25mm hex head screw, fasten it in place. This self taps into the printed part. | RRP-FISH1-080
Secure the fan and hot end wires with the cable ties. Make sure the thermistor and heater cartridge are still fully inserted in the heater block. Try to cable tie the wires to keep them as close in to the effector as possible. | RRP-FISH1-081

# Hot end wiring

CAUTION! The next step describes wiring up the hot end connector. GREAT CARE should be taken doing this. The heater cartridge and the fan wires have 19V running through them ALL THE TIME. The thermistor wires are 3.3V, and connect directly to the Arduino chip on the Duet. If you incorrectly wire the plug, a short circuit between the thermistor wires and any of the other wires MAY DESTROY YOUR DUET!

## Wiring diagram

NOTE: The wiring diagram below, and pictures, show RED heater cartridge wires. Yours will be WHITE.

reprappro-hotend-connections

Put the pins on the ends of the wires into the six-way female socket. The wiring diagram, above, is looking into the back of the socket, where you insert the crimps. The little black rectangle is the locking tab, and the housing has small embossed ‘1’ and ‘6’ numbers on it, so you can orientate it as the diagram. The pins are crimped on one side, and smooth on the other. The smooth sides go downwards in the diagram. | ORM-HotEndBuild-43
Neither the thermistor nor the heater cartridge have a polarity so it doesn’t matter which way round their wires go. (Though the H+ and H- are the way that the machine will apply power – hence the labels.) Make sure to get the polarity of the fan right. This picture shows one of the fan wires being put into the housing, but it is not fully in yet; you can’t see the crimp easily when it is. | ORM-HotEndBuild-44
Check that the pins are all the same depth into the housing. The pins are very difficult to remove without damaging them, so check twice, plug in once! They should click into place, and then shouldn’t easily push further through, or pull back out. | ORM-HotEndBuild-45

## Wire colours, related to hot end wiring loom

Wiring loom | Hot end wires
1 Yellow | Red FAN wire (+19V)
2 White | Black FAN wire (ground)
3 Green | Thermistor wire (green/blue/yellow, 3.3V)
4 Blue | Thermistor wire (green/blue/yellow, 3.3V)
5 Purple | Thick WHITE heater wire (+19V)

5 Black
6 Red | Thick WHITE heater wire (ground)

6 Brown

You can check the wire order by comparing it to the end of the hot end loom, which the hot end plugs into. | RRP-FISH1-082

# Mounting the effector

Orientate the effector so the fan is facing the open side of the printer. As you did when connecting the rods to the carriages, gently prise the rod ends apart, and slip them over the balls of the effector. Tighten the grip of the rods on the stainless steel balls, by tightening the M3x8mm cap head screws on the rods. | RRP-FISH1-083
The printer so far. | RRP-FISH1-084

Fisher Delta 3D printer © 2016. All Rights Reserved.

Powered by WordPress (http://www.wordpress.org). Designed by Woo Themes (http://www.woothemes.com)

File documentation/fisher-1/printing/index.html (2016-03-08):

# Printing

# First Print

The microSD image contains a sample print: Robot.g which makes for a fun first print. Here is a suggested workflow from powering on the Fisher 3D printer.

Click on heater 1 to heat up the nozzle (or send ‘T0‘). The hot end active temperature is set to 200C in the config.g with the line: G10 P0 S200 R0 ; Set tool 0 operating and standby temperatures You can also set the temperature manually by entering the appropriate value. If you want to turn off the hot end, click on heater 1 again to set it to ‘standby’ (or send ‘T99‘). | fisher-heater1-button
Click on Home All (or send ‘G28‘). | fisher-homeall-button
Click on Auto Bed Compensation (or send ‘G32‘). | fisher-compensation-button
Navigate to the G-Code Files tab and click on Robot.g to print it. If you’re connecting to your printer via USB, and using Pronterface, select SD > SD print and select ‘robot.g’. | robot-file

# Preparing your own files for printing

Having celebrated your success and shown all of your friends and family, you will need one more piece of software to enable you to prepare 3D models for printing. Please follow the instructions given here (https://reprappro.com/documentation/commissioning-introduction/printing-duet/).

Fisher Delta 3D printer © 2016. All Rights Reserved.

Powered by WordPress (http://www.wordpress.org). Designed by Woo Themes (http://www.woothemes.com)

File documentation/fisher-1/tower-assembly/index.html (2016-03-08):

# Tower assembly

# Goal

By the end of this section, you will have completed the towers. | RRP-FISH1-037

# Carriage

The carriage runs on the towers, and three of them combine to move the effector, which carries the hot end, that prints parts. You will need the following parts:

# | Component | Qty | Type

1304 | Carriage | 1 | Printed
112 | M3x25mm cap head screw | 1 | Fastener
242 | M3x16mm cap head screw | 2 | Fastener
204 | M3 Nylock nut | 2 | Fastener
212 | M3 plain washer | 2 | Fastener
258 | M3 nut | 1 | Fastener
1191 | 6mm threaded steel ball | 2 | Fastener
287 | LM8UU linear bearing | 1 | Hardware
1182 | LM8LUU linear bearing | 1 | Hardware

RRP-FISH1-015

## Connecting rod joints

Using an M3x16mm cap head screw, fit this into the carriage as shown. Put an M3 plain washer, then an M3 Nylock nut, to hold it in place. | RRP-FISH1-018
Place the second M3x16mm cap head screw in the other side, secured with an M3 plain washer and M3 Nylock nut. This screw can be hard to access. It’s very handy to have a ball-ended Allen key, as this can hold the screw at an angle. | RRP-FISH1-019
But you can do the same thing with a normal Allen key, using the short side. Alternatively, cut down the Allen key, to make it easier to access the cap head screw. | RRP-FISH1-020
Make sure the screws are straight and level. If they are not, this may distort the print. The nyloc nut and washer should force the screw straight. Tighten them so there is no movement in the screw. This shouldn’t need to be really tight, just pinched up. | RRP-FISH1-021

Screw on a 6mm threaded steel ball to each side. Before fitting, make sure the balls are free from swarf inside, and that they are threaded (spares are supplied if you have one or two that are not threaded). Fully screw the balls on, then check that the outside measurement of the balls is close (+/- 0.25mm for best accuracy) to 56mm. You can tighten the Nyloc on the screw to pull the ball out a little, if necessary. If too wide, remove the ball and file down the screw a little, then replace the ball and measure.
NOTE: Kits supplied after 1st November 2015 have steel balls that are not tapped as deeply as previous versions. The the outside measurement with these balls will be a little wider, at around 57mm.

RRP-FISH1-022

The precise distance between the balls is actually not that important. What is important is that the distance between the balls on the carriage, and those on the effector (see later in the instructions) should be the same, as close as possible. The rods that connect the carriage and effector must be parallel, so that the movement of the effector is always square to the carriage. If the distance between the balls is not the same, the rods will not be parallel, and the movement of the effector and hot end will not be consistent, and you may end up printing parts that are not dimensionally accurate.

## Linear bearings

Drop the M3 plain nut into the nut trap in the centre of the carriage. | RRP-FISH1-016
Screw in the M3x25mm cap head screw from the front of the part. Don’t tighten it yet. | RRP-FISH1-017
Slide in the two 8mm linear bearings as shown. Note the orientation. | RRP-FISH1-023
The short bearing should have equal amounts of it showing above and below the carriage. The long bearing should be set at roughly the same height as the short bearing, on the top. Tighten the M3x25mm cap head screw to hold them in place. | RRP-FISH1-024

## Repeat, then fit

Build two more exactly the same. Before continued use, the balls should be locked onto the threads with an effective thread locking compound (such as Loctite, or we find superglue works very well although one has to be careful, and quick, screwing the ball on). If you prefer to leave this until the machine is built, in case you need to go back and fix build errors, then leave until after the commissioning stage (which includes a reminder). | RRP-FISH1-025
Slide each carriage onto a tower, with the balls inwards, and the longest bearing on the right, downwards, as shown. | RRP-FISH1-026

# Idler bracket assembly

The idler bracket is at the top of the tower, and provide the bearing around which the belt will go, which drives the carriage. You will need the following parts:

# | Component | Qty | Type

1285 | Idler bracket | 1 | Printed
1243.1 | Idler | 1 | Printed
242 | M3x16mm cap head screw | 5 | Fastener
258 | M3 nut | 5 | Fastener
212 | M3 plain washer | 2 | Fastener
279 | 623 bearing | 2 | Hardware

RRP-FISH1-027

## Idler

Assemble the idler bearing in this order: M3x16mm cap head screw, M3 plain washer, 2 x 623 bearing, M3 plain washer, M3 nut. | RRP-FISH1-028
Tighten this up, but check that the 623 bearings can rotate freely. If they stick, try turning the washer around. These tend to have a rounded side and a more flat side; put the rounded side towards the bearing. | RRP-FISH1-029
Push the idler bearing assembly into the printed idler part. The two side are different, with a seat for the M3 nut on one side, and for the screw head on the other. | RRP-FISH1-030
Make sure the idler bearing assembly is seated fully in, and the bearings are level with the idler printed part. | RRP-FISH1-031

## Idler bracket

Push two M3x16mm cap head screws through the idler bracket, as shown. | RRP-FISH1-032
Push an M3 nut into each recess in the idler printed part. Screw the idler up into the recess in the idler bracket. This will later be used to tension the drive belts, so may be left loose at this stage. | RRP-FISH1-033
Drop an M3 nut into the nut trap recess, and screw in the last two M3x16mm cap head screws as shown. These will hold the top of the side panels, so again, leave these loose at this stage. | RRP-FISH1-034

## Repeat, then fit, again

Build two more idler brackets, exactly like the first. | RRP-FISH1-035
Fit them, one on each tower, as shown. The smooth rod should be flush with the surface of the idler bracket. | RRP-FISH1-036
The printer so far. | RRP-FISH1-037

Fisher Delta 3D printer © 2016. All Rights Reserved.

Powered by WordPress (http://www.wordpress.org). Designed by Woo Themes (http://www.woothemes.com)

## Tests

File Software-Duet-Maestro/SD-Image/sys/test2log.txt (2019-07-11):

2013-01-04 11:50:09 Event logging started
2013-01-04 11:50:11 Error: Temperature reading fault on heater 1: sensor open circuit
2013-01-04 11:50:11 Error: Temperature reading fault on heater 2: sensor open circuit
2013-01-04 11:51:25 Event logging stopped
2019-06-04 13:07:42 Event logging started
2019-06-04 13:08:06 Event logging stopped

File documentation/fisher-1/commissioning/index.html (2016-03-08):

# Commissioning

# Power on checks

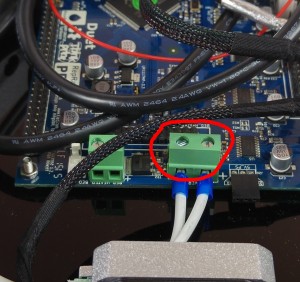
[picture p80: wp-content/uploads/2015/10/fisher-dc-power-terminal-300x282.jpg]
fisher-dc-power-terminal
Before applying 19v to the machine, confirm there is no short in the dc power circuit by measuring the resistance between the screws of the power input screw terminal. There should be very high resistance, or infinite resistance, ie no connection, between these two terminals. | 

Now connect the power supply to the machine, power it on and make sure the 19v head fan comes on. If it does not, TURN OFF THE PRINTER IMMEDIATELY, and check your wiring. Otherwise, wait a few moments (maximum 20 seconds) and check for overheating of the nozzle. At this stage, the nozzle should remain at room temperature, so if you see smoke emanate from the nozzle, switch the machine off IMMEDIATELY and check your wiring. If the hot end does heat up, you have most probably wired the hot end connector incorrectly, with the hot end heater being connected to the fan output. So rather than the fan being on all the time, the heater is on all the time.

# First connection

Download the microSD card image, extract and copy to the microSD card, then push it into the socket in the Duet. As the Duet is upside down in the machine, the microSD card should be inserted with the contacts face up, until it clicks. | Fisher_1_171015 (https://reprappro.com/wp-content/uploads/2015/10/Fisher_1_171015.zip)
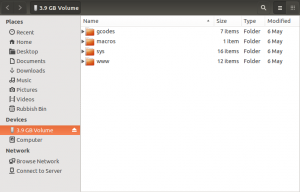
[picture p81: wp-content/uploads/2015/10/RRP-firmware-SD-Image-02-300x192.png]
RRP-firmware-SD-Image-02
The folder structure on your microSd card should look like the screenshot. | 
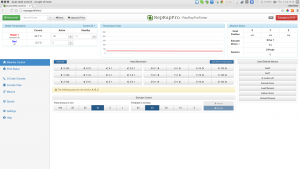
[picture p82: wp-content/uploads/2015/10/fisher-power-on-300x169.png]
fisher-power-on
Connect ethernet and power to the machine. Open a web browser and navigate to: http://reprapprofisher The web interface will automatically connect if the machine is found. If this is not the case, please see the troubleshooting guide. | 
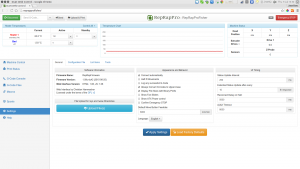
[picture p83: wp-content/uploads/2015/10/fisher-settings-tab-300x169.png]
fisher-settings-tab
Navigate to the Settings tab and verify the firmware version, which currently should be 1.09c-dc42 (2015-06-25). If you have 1.09, update your firmware using RepRapFirmware-1.09c-dc42 (https://reprappro.com/wp-content/uploads/2015/07/RepRapFirmware-1.09c-dc42.txt) Change the extension to .bin, then flash as per the instructions here (https://reprappro.com/documentation/commissioning-introduction/maintenance-duet/#RepRapPro_Firmware). | 
By default, the Duet is set up to get it’s IP address by DHCP (ip address is set to 0.0.0.0 in config.g, to enable this). You can set up the Duet on you network a number of other ways; see here (https://reprappro.com/documentation/commissioning-introduction/commissioning-duet/). If you are having problems connecting via Ethernet, see the troubleshooting section here (https://reprappro.com/documentation/troubleshooting-introduction/hardware-problems/).

If you cannot connect by ethernet, you can run your Fisher from the USB port. Follow the instructions from the general Duet commissioning (https://reprappro.com/documentation/commissioning-introduction/commissioning-duet/), which will guide you through setting up communication and connecting. These instructions are for our other, non-Delta printers (Huxley Duo, Mendel 3 and Ormerod), so once connected in ‘Pronterface’, come back and follow the instructions in the following sections. Continue to use the SD Image for Fisher, from the first step above; do not use one of the other SD Images listed in the commissioning instructions, they will not run the Fisher correctly.

# Axis motion

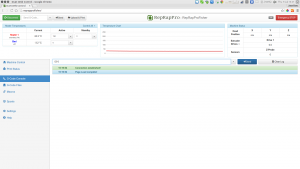
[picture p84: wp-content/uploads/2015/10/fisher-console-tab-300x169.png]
fisher-console-tab
Next test motion of the axes. Navigate to the console tab, then set incremental mode by entering and sending the following code: G91 Move all carriages to roughly half way up the bars, then command each axis in turn and confirm an upwards movement of 10mm for each. G1 S2 X10 F500 G1 S2 Y10 F500 G1 S2 Z10 F500 If a carriage moves down, rather than up, power off the printer, and reverse the motor wiring connection for that axis on the Duet. | 

# End stops

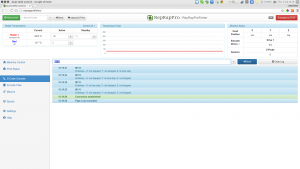
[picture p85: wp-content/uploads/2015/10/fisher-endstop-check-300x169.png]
fisher-endstop-check
Now confirm the machine registers triggering of the endstops. Navigate to the console tab, then send a command to check the status of the endstops (see picture): M119 The response should be: Endstops - X: not stopped, Y: not stopped, Z: not stopped Trigger the X endstop (the one nearest the first motor which moved in the previous test) by holding down the lever with a finger, and send the command again. The response should be: Endstops - X: at max stop, Y: not stopped, Z: not stopped Repeat this procedure for the other two endstops, and check that their state changes. | 
If the response is not correct, check your wiring. Check that the endstop wires are connected to the outer two pins of each microswitch, and not the central pin. Check that the correct endstop is connected to the correct place on the Duet (see the wiring diagram).

You can also check the endstops are working visually, by checking the LED lights on the Duet. Lay the Fisher on it’s side, or turn it over completely. You should see the Duet, and 5 LED lights should be lit; the USB LED (this shows the Duet is getting 5V), and the four endstop switches (see the wiring diagram HERE (https://reprappro.com/documentation/fisher-beta/electronics/#Wiring_diagram) for their location). If any are not lit, check the wiring connections. Press each endstop in turn, and check that the corresponding light goes out on the Duet. Also check the bed probe is functioning, by pressing down on the bed.

# Homing

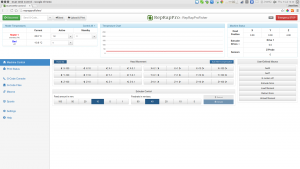
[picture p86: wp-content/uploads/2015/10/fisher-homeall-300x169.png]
fisher-homeall
Navigate back to the Machine Control tab, and click on the ‘Home All’ button (or send ‘G28’). All axes will move up until they reach the endstops, down a little and back up again slowly, then move rapidly down to rest 4mm above the print surface. | 

# Bed probing

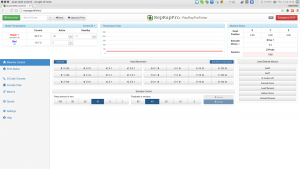
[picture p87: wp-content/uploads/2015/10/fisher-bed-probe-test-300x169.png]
fisher-bed-probe-test
Monitor the value under Z Probe in the machine status box. The value should be zero. You can also send ‘G31’ to get the current reading from the bed probing. Gently push down then release the bed near each of the mounting points in turn, and confirm the probe value changes to 1000, then returns to zero each time. | 

# Extruder drive

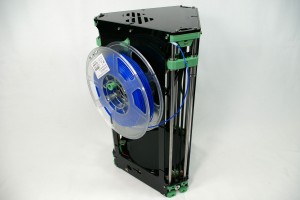
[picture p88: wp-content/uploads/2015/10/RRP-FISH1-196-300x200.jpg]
RRP-FISH1-196
Push some filament through the slot in the filament guide tube, which should feed it into the extruder drive block. Using the thumbwheel, engage the filament and feed a few centimetres through. Hold the thumbwheel and try to pull the filament back out. If it slips easily, adjust the idler tension using the M4 button head screw. | 
Enter a value of zero as the Heater 1 Active temperature. As the nozzle is still at room temperature, cold extrusion prevention must be overriden. Send the following: T0 M302 P1 Now advance the filament using the jog buttons on the Manual Control tab, until it reaches the top of the heatsink. Once satisfied the extruder drive is working, re-enable cold extrusion prevention using the following command: M302 P0 Reset the Active temperature for Heater 1 back to 190C.

# Hot end

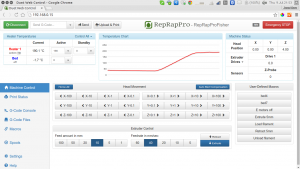
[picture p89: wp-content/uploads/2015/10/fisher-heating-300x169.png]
fisher-heating
Click on Heater 1 and monitor the temperature rise of the nozzle. | 
The final step is to check extrusion. The extruder drive motor will be enabled, so send the following command to put it into an idle state: M84 E0 Using the thumbwheel, feed the filament into the hot end and extrude a couple of centimetres. With a steady feed, the filament should extrude without too much resistance. | fisher-extrusion-test

# Prepare for printing

Your RepRap Fisher 3D printer is now almost ready for its first print. Check the following before proceeding…

Filament spool is loaded. Threaded balls are locked and lubricated. Belts are equally tensioned. Top panel is fitted. Bed is in place. | fisher-spool-mounted

Fisher Delta 3D printer © 2016. All Rights Reserved.

Powered by WordPress (http://www.wordpress.org). Designed by Woo Themes (http://www.woothemes.com)

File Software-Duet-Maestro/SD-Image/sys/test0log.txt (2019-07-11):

2013-01-04 11:49:02 Event logging started
2013-01-04 11:49:11 Event logging stopped

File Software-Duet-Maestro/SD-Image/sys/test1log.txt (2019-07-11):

2013-01-04 11:51:25 Event logging started
2013-01-04 11:52:06 Event logging stopped
2019-06-04 13:08:06 Event logging started
2019-06-04 13:08:35 HTTP client 192.168.1.104 disconnected

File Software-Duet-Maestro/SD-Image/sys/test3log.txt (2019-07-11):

2013-01-04 11:49:11 Event logging started
2013-01-04 11:50:09 Event logging stopped
2019-06-04 13:07:21 Event logging started
2019-06-04 13:07:42 Event logging stopped

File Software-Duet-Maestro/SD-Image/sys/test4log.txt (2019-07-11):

2013-01-04 11:52:06 Event logging started

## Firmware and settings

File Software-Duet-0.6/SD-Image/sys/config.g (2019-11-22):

; Configuration file for RepRap Ltd Fisher - delta 3D printer

; Communication and general
M111 S0                             ; Debug off
M550 Pfisher1                       ; Machine name (can be anything you like)
M551 Preprap                        ; Machine password (used for FTP)
M540 P0xBE:0xEF:0xDE:0xAD:0xFE:0xFD ; MAC Address
;*** Adjust the IP address and gateway in the following lines to suit your network
M552 P0.0.0.0 S1                    ; DHCP IP address
;M552 P192.168.1.10                 ; Set the IP address
;M553 P255.255.255.0                ; Set netmask
;M554 P192.168.1.1                  ; Set the gateway
M555 P2                             ; Set output to look like Marlin
G21                                 ; Work in millimetres
G90                                 ; Send absolute coordinates...
M83                                 ; ...but relative extruder moves

; Axis and motor configuration
M569 P0 S1       ; Drive 0 goes forwards
M569 P1 S1       ; Drive 1 goes forwards
M569 P2 S1       ; Drive 2 goes forwards
M569 P3 S1       ; Drive 3 goes forwards
M569 P4 S1       ; Drive 4 goes forwards
M574 X2 Y2 Z2 S1 ; set endstop configuration (all endstops at high end, active high)

;*** The homed height (H150) is deliberately set too high in the following - you will adjust it during calibration
M665 R81.0 L160.0 B75 H150      ; set delta radius, diagonal rod length, printable radius and homed height
M92 X87.489 Y87.489 Z87.489     ; Set axis steps/mm
M906 X800 Y800 Z800 E800        ; Set motor currents (mA)
M201 X4000 Y4000 Z4000 E4000    ; Accelerations (mm/s^2)
M203 X15000 Y15000 Z15000 E9000 ; Maximum speeds (mm/min)
M210 Z50                        ; Homing feedrate
M566 X1200 Y1200 Z1200 E1200    ; Maximum instant speed changes mm/minute

; Thermistors and heaters
M305 P1 R4700 ; Thermistor series resistor
M140 H-1      ; Disable heatbed

; Tool definitions
M563 P0 D0 H1 ; Define tool 0
G10 P0 S200 R0 ; Set tool 0 operating and standby temperatures
;M563 P1 D1 H1 ; Define tool 1
;G10 P1 S0 R0 ; Set tool 1 operating and standby temperatures

;M563 P2 D0 H1 ; Define tool 2
;G10 P2 S0 R0 ; Set tool 2 operating and standby temperatures
;M563 P3 D1 H1 ; Define tool 3
;G10 P3 S0 R0 ; Set tool 3 operating and standby temperatures


M301 H1 P12 I0.4 D80 W180 B300 ; Set heater PID parameters
M92 E310 ; Set extruder steps per mm for geared drive
;M92 E144 ; Set extruder steps per mm for direct drive

;Define the mesh for mapping the bed
M557 R75 S20

;// Z probe and compensation definition
;*** If you have an IR zprobe instead of a switch, change P4 to P1 in the following M558 command
M558 P4 X0 Y0 Z0 H4 ; Z probe is a switch and is not used for homing any axes
G31 X0 Y0 Z0.0 P200 ; Set the zprobe height and threshold (put your own values here)

; put your endstop adjustments here
M666 X0.0 Y0.0 Z0.0

;*** If you are using axis compensation, put the figures in the following command
M556 S78 X0 Y0 Z0 ; Axis compensation here

; Put your final XY calibration figures here (see instructions).
M579 X1.0 Y1.0

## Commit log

2016-03-08 Fisher docs added.
    [1136.SLDPRT, 1178.SLDASM, 1179.SLDPRT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]
2018-06-19 Correct STL for part 1306 added.
    [#1195 - 05.DXF, #1223.DXF, 1195 - 05 - single.DXF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]
2019-01-18 Extruder drive gear with grip added.
    [1287-magnetic.DXF, 1310.1-small-gear with grip.STL, 2mm-6188.dxf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]
2019-01-22 Reorganising and updating files.
    [3DBenchy.g, INIT.g, Robot.g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]
2019-01-23 Further file tidying.
    [1243x3.g, 1245x3.g, 1247.g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]
2019-01-24 More file tidying...
    [1239.5 Cover.DXF, 1239.5 Cover.SLDPRT, 1239.5.SLDPRT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]
2019-02-01 Improved layout of config.g
    [3DBenchy.g, Robot.g, bed.g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]
2019-02-01 Reorganised files (again).
    [3DBenchy.g, Robot.g, bed.g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]
2019-04-05 MasterSpool spigot added.
    [1195 - 05 - single.1.dxf, 1249.1-masterspool-spigot.stl, masterspool-spigot.fcstd]
2019-04-08 Filament guide spacer added; spigot now secured with cap screws not countersunk.
    [1195 - 05 - single.DXF, 1195 - 05.DXF, 1195.1.dxf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]
2019-04-18 File tidying - new masterspool spigot.
    [#1195 - 05.DXF, #1223.DXF, 1249.STL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]
2019-06-18 Updated nozzle duct added.
    [1247.1 Nozzle Duct.stl, 6197-masterspool-spigot.g]
2019-06-18 Improvement to side-panel design (1302.1).
    [1302.1.dxf]
2019-06-18 Panel with rods updated too...
    [1195.1.dxf]
2019-06-18 Improvement to front panel.
    [1302.1.dxf]
2019-06-20 Fisher rod design improved (end ball holders reduced).
    [1195.1.dxf, 1195.2.dxf, 1232-fisher-rods-x2.dxf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]
2019-06-25 Extruder-drive panel updated with new rod design.
    [1196 - 07 - single.dxf, 1196 - 07.dxf, 1196.1.dxf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]
2019-07-03 Panel 1196 modified to accommodate Duet Maestro reset button.
    [1196.1.dxf, 1196.2.dxf]
2019-07-11 Tidying DXFs
    [1195.2.dxf, 1196.2.dxf, 1232.1-fisher-rods-x2.dxf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]
2019-07-11 Added InDevelopment folder.
    [1243x3.g, 1245x3.g, 1247.g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]
2019-07-24 Made mesh bed levelling standard for the Maestro release.
    [bed.g, config.g]
2019-07-26 Made mesh bed probing standard.
    [bed.g, config.g]
2019-08-19 Small design improvement to 1305.
    [1305.1.STL, 1305.1.fcstd, 1305.STL]
2019-08-19 Moved old DXF to legacy
    [1232.DXF]
2019-08-29 Organising files to support Duet 0.6 and Maestro.
    [1243x3.g, 1245x3.g, 1247.SLDPRT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]
2019-09-04 Fixed Maestro SD image
    [bed.g, config-override.g, heightmap.csv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]
2019-09-04 More updates...
    [config-override.g, config.g]
2019-09-06 Moved M666 commands to make them easier to find.
    [config.g]
2019-09-11 File tidying...
    [1243x3.g, 1245x1.g, 1245x3.g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]
2019-09-20 Fixed bug in resume.g.
    [pause.g, resume.g]
2019-11-22 Added test cross for XY scaling calibration.
    [test-cross.fcstd, test-cross.g, test-cross.stl]
2019-11-22 Added XY scaling to config files.
    [config.g]
2020-04-16 Experimental redesigns of 1243 and 1304.
    [1243.1.FCStd, 1243.1.g, 1243.1.stl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]
2020-04-24 Tidying dxf files.
    [1223.dxf, 1232.1.dxf, 1284.DXF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]
2020-05-11 Improved toothed-belt grip on part 1304.
    [1304.2.FCStd, 1304.2.g, 1304.2.stl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]
2020-05-19 New 5mm acrylic laser dxf files with position markers.
    [base-plate-1299-with-top-plate-1284-to-left.dxf, bed-1287-with-base-plate-1299-to-left.dxf, top-plate-1284.dxf]
2020-06-16 Tidying and simplifying DXFs
    [1195.2.dxf, 1195.3.dxf, 1232.1-fisher-rods-x2.dxf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]
2020-09-03 Fixed bug in E motors off macro
    [#1302.1.dxf]
2020-10-09 New design for lasercut side panel for new Duet.
    [1196.3.dxf]
2021-02-11 Tidying STLs.
    [rod-end.STL]
2021-02-16 Improved design of small extruder gear with longer grub screw and nylock M3 nut.
    [1310.2-small-gear with grip.STL, 1310.2.FCStd]
